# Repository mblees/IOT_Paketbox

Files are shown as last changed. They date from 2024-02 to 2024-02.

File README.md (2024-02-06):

# IoT-Projekt – Paketbox Dokumentation
WhatsApp Bild 2024-02-06 um 20 36 11_9b5375aa

## Übersicht:

### 1. Hardware
   #### 1.1 Box
   Das Gerüst der Paketbox besteht aus MiniTec-Aluprofilen, die zum Halten von 4 mm dicken Spanholzplatten genutzt werden. Der Deckel wird durch 2 Scharniere mit dem Körper der Box verbunden.

   #### 1.2 Sensoren/andere Hardware
   - Ultraschallsensor: HC-SR04
       - Da der Sensor auf 5V läuft und die GPIO-Pins des ESP32 nur 3,3V vertragen, muss ein Spannungsteiler bestehend aus 2 10k Ohm Widerständen verwendet werden. Das senkt die Spannung allerdings nicht genau auf 3,3V, deshalb muss in der Software damit gerechnet werden.
   - Reed-Modul: KY-021
       - Wird mit 3,3V versorgt, daher muss hier nichts Besonderes beachtet werden.
   - Schrittmotor: 28BYJ-48
       - Wird mit 5V über den dazugehörigen Motortreiber versorgt.
   - Matrixtastatur: [Link zur Tastatur](https://www.az-delivery.de/products/4x4-matrix-keypad)
       - Aufgrund mangelnder Pins verwende ich die 4x4 Matrix nur als 2x2 Matrix mit den Tasten 1, 2, 4, 5.
   - Stromversorgung durch eine Powerbank mit 5V Ausgang.

   #### 1.3 Mikroprozessor
   Beim Mikroprozessor handelt es sich um den WiFi-LoRa-32-V2 der Firma Heltec Automation mit eingebautem LoRa-Modul, Display und integrierter LED. Um Energie zu sparen, werden sowohl das Display als auch die integrierte LED nicht verwendet.

   #### 1.4 Verschlussmechanismus
   Der Verschlussmechanismus besteht aus einem Stepper Motor mit einem Zahnrad, welches einen Kolben durch 2 Ösen schiebt. Die Ösen sind jeweils am Deckel oder am Körper der Box befestigt und verhindern, wenn der Kolben ausgefahren ist, dass sich der Deckel öffnen lässt.
   
  WhatsApp Bild 2024-02-06 um 20 21 44_378a7dea

   Anmerkung: Hier handelt es sich Budgetbedingt um 3D-gedruckte Teile welche in eienr realen Anwendung nicht sicher genug wären um ein Paket mit Wert zu sichern.

### 2. Software
   #### 2.1 C++-Part / Mikroprozessorprogrammierung
   Die Programmierung des Controllers beruht auf dem Framework/Example LMIC-node von lnlp ([GitHub-Link](https://github.com/lnlp/LMIC-node)). Ich habe eine logische Steuerung in der `main()`-Funktion hinzugefügt sowie Bibliotheken für alle Peripheriekomponenten:
   - `Matrix.h`/`Matrix.cpp`: Beinhaltet das Auslesen der Matrix-Tastatur unter Verwendung der Bibliothek: `chris--a/Keypad@^3.1.1`.
   - `Reed_sensor.h`/`Reed_sensor.cpp`: Beinhaltet das Auslesen des Reed-Sensors, das über ein DigitalReed geschieht.
   - `Rfid.h`/`Rfid.cpp`: Beinhaltet Funktionen, um einen RFID-Sensor zu verwenden. Diese Funktion wurde letztendlich nicht genutzt, da der Mikrocontroller nicht genug Pins übrig hat.
   - `Stepper.h`/`Stepper.cpp`: Beinhaltet die Ansteuerung des Schrittmotor-Treibers unter Verwendung der Bibliothek: `waspinator/AccelStepper@^1.64`.
   - `Supersonic_sensor.h`/`Supersonic_sensor.cpp`: Beinhaltet das Auswerten des Ultraschallsensors und eine Funktion, die einen Mittelwert bildet, da der Sensor ab und zu falsche Werte liefern kann.

   #### 2.2 Python Service
   Der Service nutzt die HomeAssistantAPI, um Push-Benachrichtigungen an Handys zu schicken und die `paho-mqtt`-Bibliothek, um die von TTN empfangenen LoRa-Daten auszuwerten und daraufhin einen `notify`-Service in HomeAssistant auszulösen.
   
   notify

   #### 2.3 HomeAssistant
   Der HomeAssistant Server läuft in meinem Fall auf einer Oracle VM VirtualBox auf dem selben PC auf welchem auch der Python Service läuft. Die beiden Programme sind allerdings nur in soweit anhängig voneienander, dass sie im selben Wlan ausgeführt werden müssen.
   
   

### 3. Datenübertragung
   Die Daten, die mit den Sensoren erfasst werden, werden beim Öffnen und Schließen der Box vom Mikrocontroller über LoRa und The Things Network (TTN) gesendet. TTN stellt die Daten über einen MQTT-Server zur Verfügung, welche wir mithilfe eines Python-Services abfangen und daraufhin einen Service in HomeAssistant auslösen. Der Service in HomeAssistant führt dann wiederum dazu, dass eine Push-Benachrichtigung auf dem Handy des Besitzers der Box erscheint.

   Sensoren -> ESP32 -> LoRa -> TTN -> MQTT -> Python Service -> HomeAssistant -> Mobiltelefon

### 4. Pinbelegung


| Gerät | Pins |
|---|---|
| Matrixtastatur | 0, 2, 23, 25 |
| Steppermotor | 12, 13, 17, 21 |
| Reed Sensor | 36 |
| Ultraschallsensor | 22, 37 |
| LoRa Modul (Werk) | 19, 18, 5, 15, 4, 16, 26, 27, 14 |

### 5. Anmerkungen
Um weitere Features wie einen RFID-Sensor hinzuzufügen, fehlen dem verwendeten ESP32 weitere Pins. Eine mögliche Alternative war in diesem Fall der STM-WL55JC mit LoRa-Antenne. Allerdings gibt es für diesen Mikrocontroller keine öffentlichen LoRa-Bibliotheken, die für dieses Projekt in Frage gekommen wären. Ich habe versucht, eine Bibliothek für diesen Controller selbst zu schreiben, habe aber nach einigen Stunden Arbeit keine Ergebnisse erzielen können.

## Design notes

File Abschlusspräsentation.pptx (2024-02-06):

## Paketbox

Marius Blees

## Übersicht

- Hardware
- Software
- Datenübertragung
- Vorführung

Paketbox

## Hardware

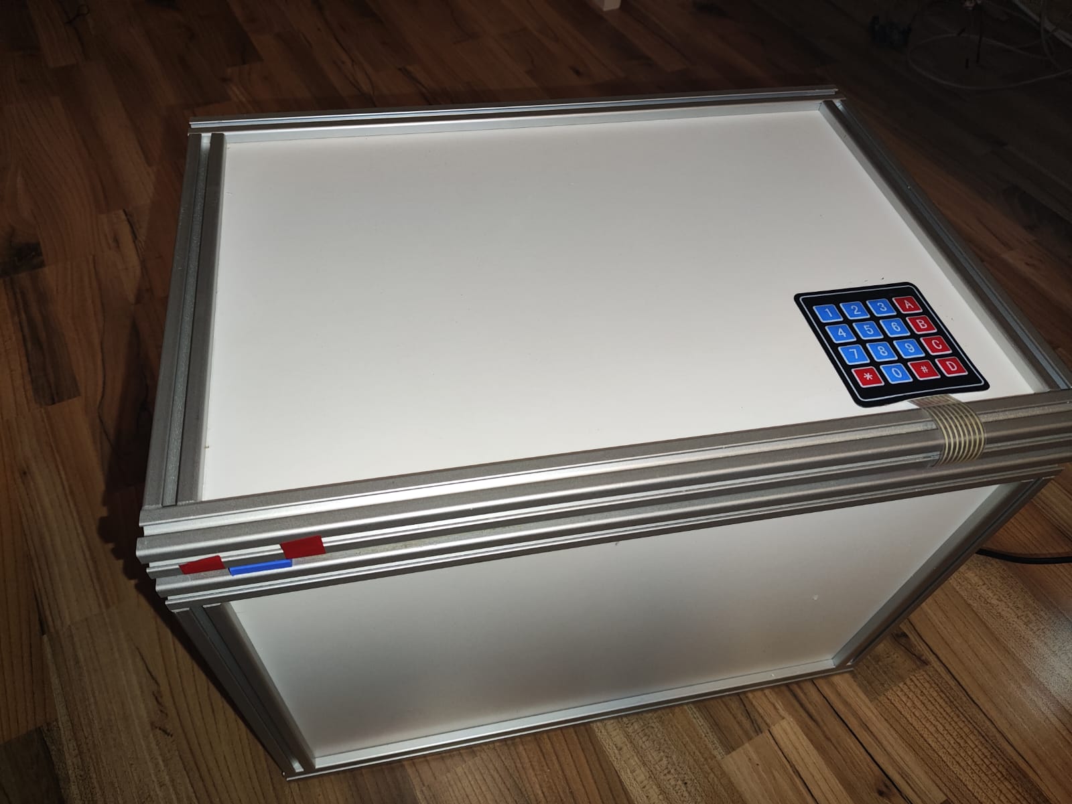
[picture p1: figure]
efe

Finales Aussehen der Paketbox

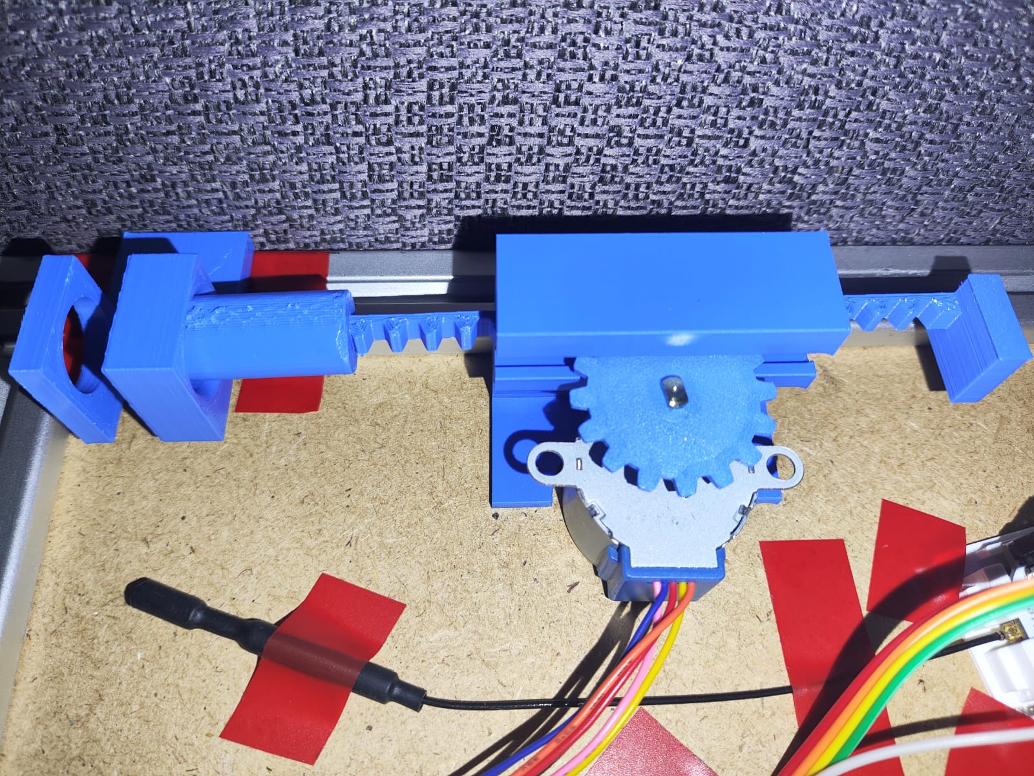
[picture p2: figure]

Verschlussmechanismus

## Hardware

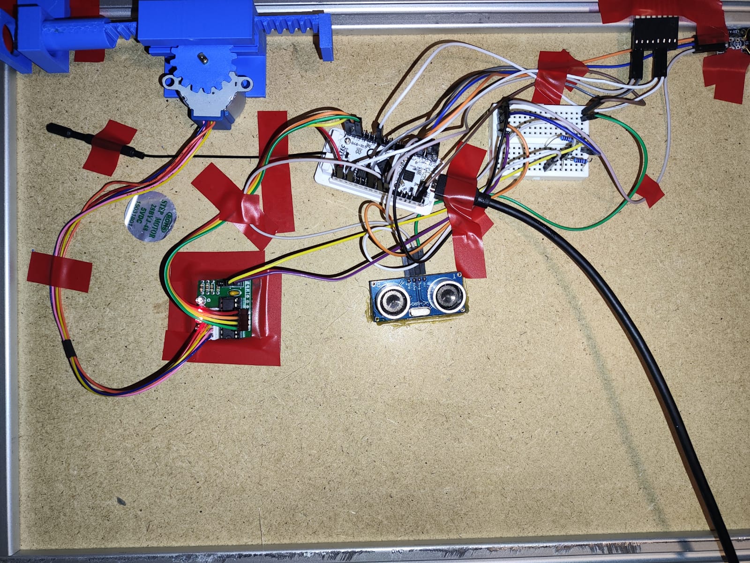
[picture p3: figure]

Verkabelung der Sensoren/Komponenten

## Software

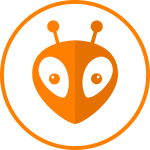
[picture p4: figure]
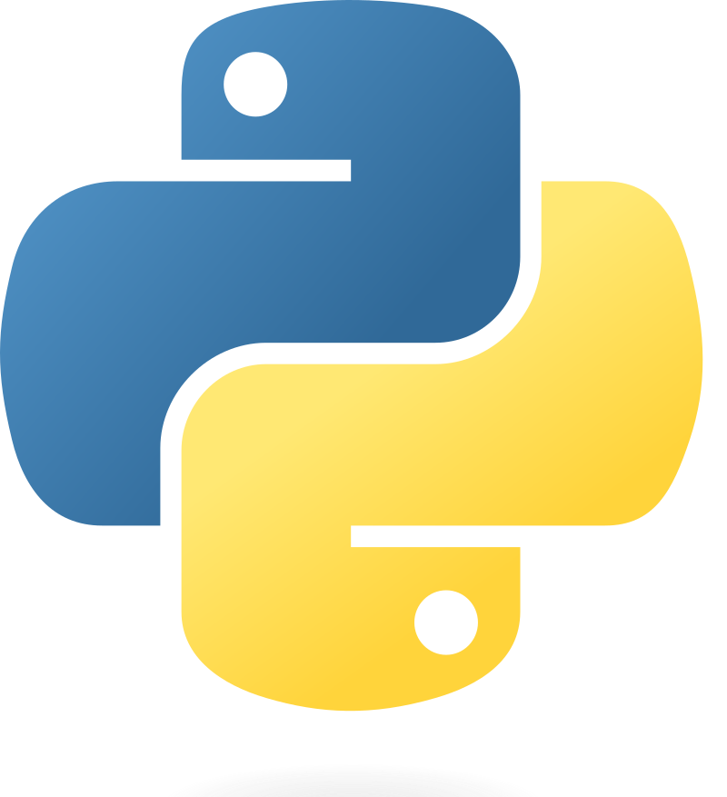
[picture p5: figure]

PlatformIO:
Programmierung in C++/ Arduino

Python:
als Service und Schnittstelle
zu HomeAssistant

## Datenübertragung

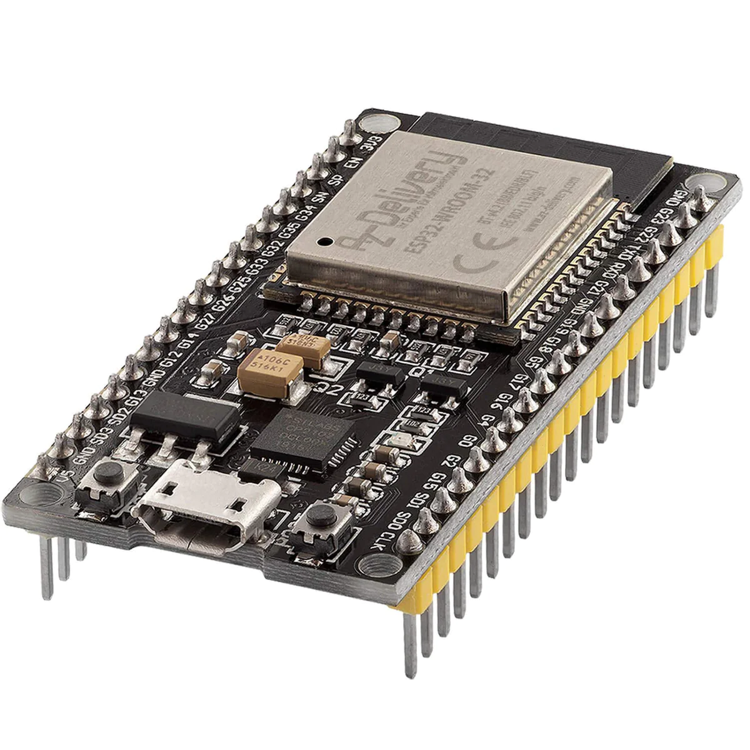
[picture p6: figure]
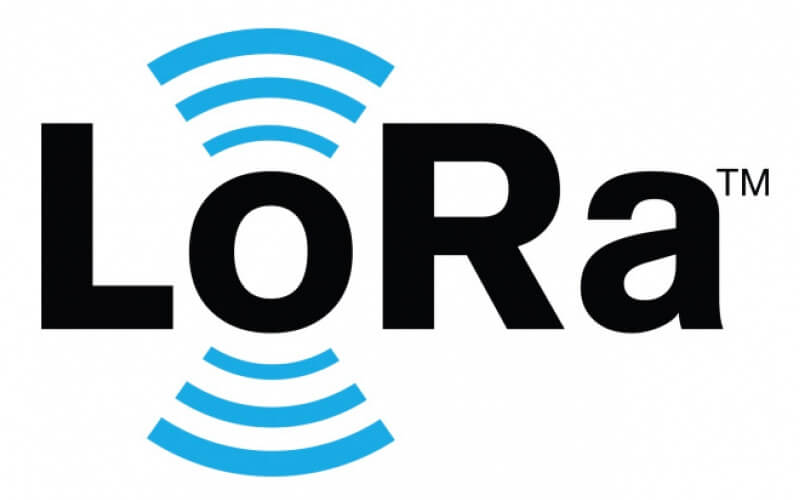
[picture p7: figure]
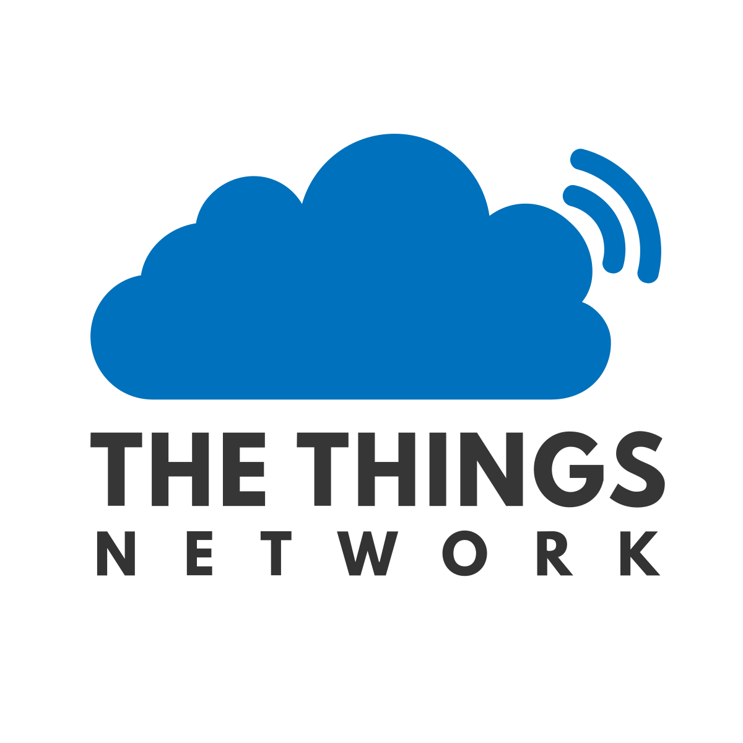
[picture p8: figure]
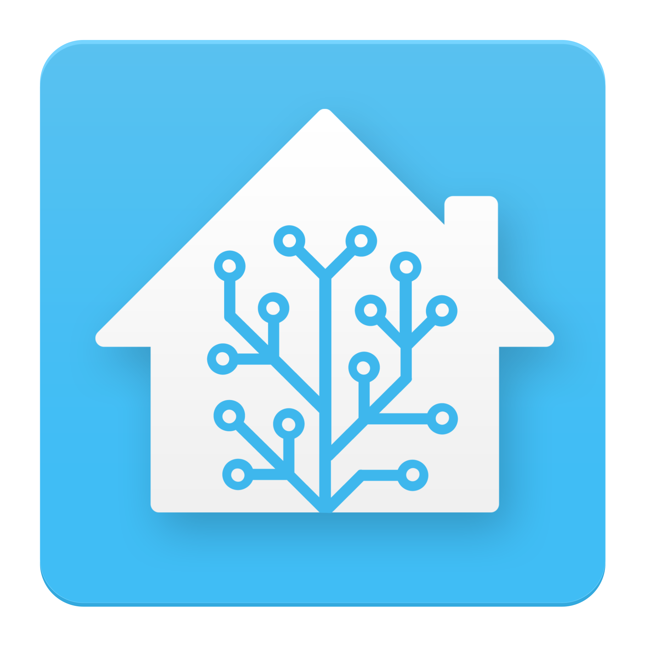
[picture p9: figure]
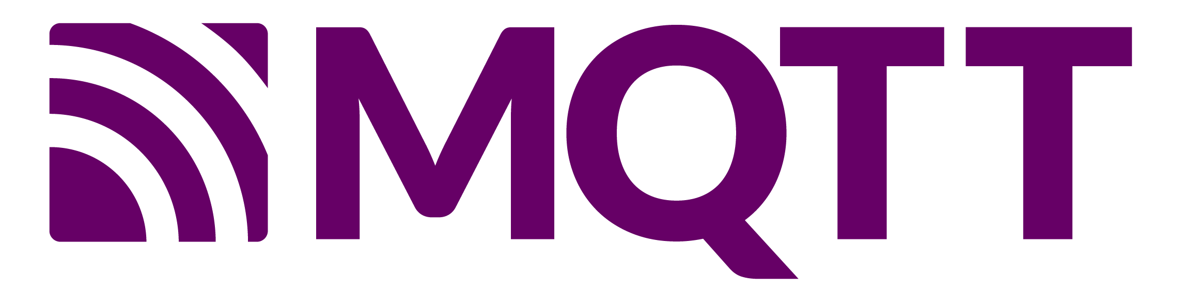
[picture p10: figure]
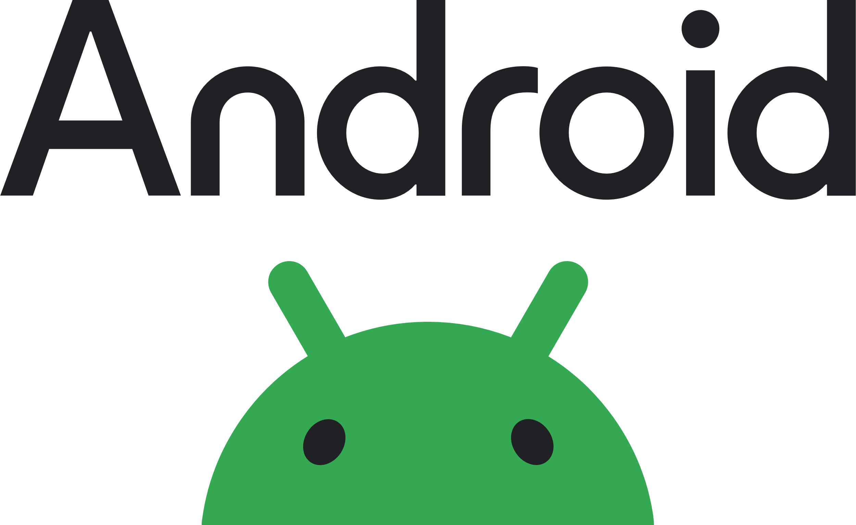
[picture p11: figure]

## VIELEN DANK

Gibt es noch Fragen?

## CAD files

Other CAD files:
Inventor/Adapter Stepper.ipt
Inventor/Connector MiniTec Counter.ipt
Inventor/Connector MiniTec.ipt
Inventor/Lineartranslator.ipt
Inventor/Schiene.ipt

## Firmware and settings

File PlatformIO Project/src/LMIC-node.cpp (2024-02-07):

/*******************************************************************************
 *
 *  File:          LMIC-node.cpp
 * 
 *  Function:      LMIC-node main application file.
 * 
 *  Copyright:     Copyright (c) 2021 Leonel Lopes Parente
 *                 Copyright (c) 2018 Terry Moore, MCCI
 *                 Copyright (c) 2015 Thomas Telkamp and Matthijs Kooijman
 *
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
 *                 THE SOFTWARE IS PROVIDED "AS IS", WITHOUT ANY WARRANTY.
 * 
 *  License:       MIT License. See accompanying LICENSE file.
 * 
 *  Author:        Leonel Lopes Parente
 * 
 *  Description:   To get LMIC-node up and running no changes need to be made
 *                 to any source code. Only configuration is required
 *                 in platform-io.ini and lorawan-keys.h.
 * 
 *                 If you want to modify the code e.g. to add your own sensors,
 *                 that can be done in the two area's that start with
 *                 USER CODE BEGIN and end with USER CODE END. There's no need
 *                 to change code in other locations (unless you have a reason).
 *                 See README.md for documentation and how to use LMIC-node.
 * 
 *                 LMIC-node uses the concepts from the original ttn-otaa.ino 
 *                 and ttn-abp.ino examples provided with the LMIC libraries.
 *                 LMIC-node combines both OTAA and ABP support in a single example,
 *                 supports multiple LMIC libraries, contains several improvements
 *                 and enhancements like display support, support for downlinks,
 *                 separates LoRaWAN keys from source code into a separate keyfile,
 *                 provides formatted output to serial port and display
 *                 and supports many popular development boards out of the box.
 *                 To get a working node up and running only requires some configuration.
 *                 No programming or customization of source code required.
 * 
 *  Dependencies:  External libraries:
 *                 MCCI LoRaWAN LMIC library  https://github.com/mcci-catena/arduino-lmic
 *                 IBM LMIC framework         https://github.com/matthijskooijman/arduino-lmic  
 *                 U8g2                       https://github.com/olikraus/u8g2
 *                 EasyLed                    https://github.com/lnlp/EasyLed
 *
 ******************************************************************************/

#include "LMIC-node.h"


//  █ █ █▀▀ █▀▀ █▀▄   █▀▀ █▀█ █▀▄ █▀▀   █▀▄ █▀▀ █▀▀ ▀█▀ █▀█
//  █ █ ▀▀█ █▀▀ █▀▄   █   █ █ █ █ █▀▀   █▀▄ █▀▀ █ █  █  █ █
//  ▀▀▀ ▀▀▀ ▀▀▀ ▀ ▀   ▀▀▀ ▀▀▀ ▀▀  ▀▀▀   ▀▀  ▀▀▀ ▀▀▀ ▀▀▀ ▀ ▀
#include "reed_sensor.h"
#include "supersonic_sensor.h"
#include "rfid.h"
#include "stepper.h"
#include "matrix.h"

const uint8_t payloadBufferLength = 4;    // Adjust to fit max payload length


//  █ █ █▀▀ █▀▀ █▀▄   █▀▀ █▀█ █▀▄ █▀▀   █▀▀ █▀█ █▀▄
//  █ █ ▀▀█ █▀▀ █▀▄   █   █ █ █ █ █▀▀   █▀▀ █ █ █ █
//  ▀▀▀ ▀▀▀ ▀▀▀ ▀ ▀   ▀▀▀ ▀▀▀ ▀▀  ▀▀▀   ▀▀▀ ▀ ▀ ▀▀ 

bool sendNotfication = false;
uint8_t payloadBuffer[payloadBufferLength];
static osjob_t doWorkJob;
uint32_t doWorkIntervalSeconds = DO_WORK_INTERVAL_SECONDS;  // Change value in platformio.ini

// Note: LoRa module pin mappings are defined in the Board Support Files.

// Set LoRaWAN keys defined in lorawan-keys.h.
#ifdef OTAA_ACTIVATION
    static const u1_t PROGMEM DEVEUI[8]  = { OTAA_DEVEUI } ;
    static const u1_t PROGMEM APPEUI[8]  = { OTAA_APPEUI };
    static const u1_t PROGMEM APPKEY[16] = { OTAA_APPKEY };
    // Below callbacks are used by LMIC for reading above values.
    void os_getDevEui (u1_t* buf) { memcpy_P(buf, DEVEUI, 8); }
    void os_getArtEui (u1_t* buf) { memcpy_P(buf, APPEUI, 8); }
    void os_getDevKey (u1_t* buf) { memcpy_P(buf, APPKEY, 16); }    
#else
    // ABP activation
    static const u4_t DEVADDR = ABP_DEVADDR ;
    static const PROGMEM u1_t NWKSKEY[16] = { ABP_NWKSKEY };
    static const u1_t PROGMEM APPSKEY[16] = { ABP_APPSKEY };
    // Below callbacks are not used be they must be defined.
    void os_getDevEui (u1_t* buf) { }
    void os_getArtEui (u1_t* buf) { }
    void os_getDevKey (u1_t* buf) { }
#endif


int16_t getSnrTenfold()
{
    // Returns ten times the SNR (dB) value of the last received packet.
    // Ten times to prevent the use of float but keep 1 decimal digit accuracy.
    // Calculation per SX1276 datasheet rev.7 §6.4, SX1276 datasheet rev.4 §6.4.
    // LMIC.snr contains value of PacketSnr, which is 4 times the actual SNR value.
    return (LMIC.snr * 10) / 4;
}


int16_t getRssi(int8_t snr)
{
    // Returns correct RSSI (dBm) value of the last received packet.
    // Calculation per SX1276 datasheet rev.7 §5.5.5, SX1272 datasheet rev.4 §5.5.5.

    #define RSSI_OFFSET            64
    #define SX1276_FREQ_LF_MAX     525000000     // per datasheet 6.3
    #define SX1272_RSSI_ADJUST     -139
    #define SX1276_RSSI_ADJUST_LF  -164
    #define SX1276_RSSI_ADJUST_HF  -157

    int16_t rssi;

    #ifdef MCCI_LMIC

        rssi = LMIC.rssi - RSSI_OFFSET;

    #else
        int16_t rssiAdjust;
        #ifdef CFG_sx1276_radio
            if (LMIC.freq > SX1276_FREQ_LF_MAX)
            {
                rssiAdjust = SX1276_RSSI_ADJUST_HF;
            }
            else
            {
                rssiAdjust = SX1276_RSSI_ADJUST_LF;   
            }
        #else
            // CFG_sx1272_radio    
            rssiAdjust = SX1272_RSSI_ADJUST;
        #endif    
        
        // Revert modification (applied in lmic/radio.c) to get PacketRssi.
        int16_t packetRssi = LMIC.rssi + 125 - RSSI_OFFSET;
        if (snr < 0)
        {
            rssi = rssiAdjust + packetRssi + snr;
        }
        else
        {
            rssi = rssiAdjust + (16 * packetRssi) / 15;
        }
    #endif

    return rssi;
}


void printEvent(ostime_t timestamp, 
                const char * const message, 
                PrintTarget target = PrintTarget::All,
                bool clearDisplayStatusRow = true,
                bool eventLabel = false)
{
    #ifdef USE_DISPLAY 
        if (target == PrintTarget::All || target == PrintTarget::Display)
        {
            display.clearLine(TIME_ROW);
            display.setCursor(COL_0, TIME_ROW);
            display.print(F("Time:"));                 
            display.print(timestamp); 
            display.clearLine(EVENT_ROW);
            if (clearDisplayStatusRow)
            {
                display.clearLine(STATUS_ROW);    
            }
            display.setCursor(COL_0, EVENT_ROW);               
            display.print(message);
        }
    #endif  
    
    #ifdef USE_SERIAL
        // Create padded/indented output without using printf().
        // printf() is not default supported/enabled in each Arduino core. 
        // Not using printf() will save memory for memory constrainted devices.
        String timeString(timestamp);
        uint8_t len = timeString.length();
        uint8_t zerosCount = TIMESTAMP_WIDTH > len ? TIMESTAMP_WIDTH - len : 0;

        if (target == PrintTarget::All || target == PrintTarget::Serial)
        {
            printChars(serial, '0', zerosCount);
            serial.print(timeString);
            serial.print(":  ");
            if (eventLabel)
            {
                serial.print(F("Event: "));
            }
            serial.println(message);
        }
    #endif   
}           

void printEvent(ostime_t timestamp, 
                ev_t ev, 
                PrintTarget target = PrintTarget::All, 
                bool clearDisplayStatusRow = true)
{
    #if defined(USE_DISPLAY) || defined(USE_SERIAL)
        printEvent(timestamp, lmicEventNames[ev], target, clearDisplayStatusRow, true);
    #endif
}


void printFrameCounters(PrintTarget target = PrintTarget::All)
{
    #ifdef USE_DISPLAY
        if (target == PrintTarget::Display || target == PrintTarget::All)
        {
            display.clearLine(FRMCNTRS_ROW);
            display.setCursor(COL_0, FRMCNTRS_ROW);
            display.print(F("Up:"));
            display.print(LMIC.seqnoUp);
            display.print(F(" Dn:"));
            display.print(LMIC.seqnoDn);        
        }
    #endif

    #ifdef USE_SERIAL
        if (target == PrintTarget::Serial || target == PrintTarget::All)
        {
            printSpaces(serial, MESSAGE_INDENT);
            serial.print(F("Up: "));
            serial.print(LMIC.seqnoUp);
            serial.print(F(",  Down: "));
            serial.println(LMIC.seqnoDn);        
        }
    #endif        
}      


void printSessionKeys()
{    
    #if defined(USE_SERIAL) && defined(MCCI_LMIC)
        u4_t networkId = 0;
        devaddr_t deviceAddress = 0;
        u1_t networkSessionKey[16];
        u1_t applicationSessionKey[16];
        LMIC_getSessionKeys(&networkId, &deviceAddress, 
                            networkSessionKey, applicationSessionKey);

        printSpaces(serial, MESSAGE_INDENT);    
        serial.print(F("Network Id: "));
        serial.println(networkId, DEC);

        printSpaces(serial, MESSAGE_INDENT);    
        serial.print(F("Device Address: "));
        serial.println(deviceAddress, HEX);

        printSpaces(serial, MESSAGE_INDENT);    
        serial.print(F("Application Session Key: "));
        printHex(serial, applicationSessionKey, 16, true, '-');

        printSpaces(serial, MESSAGE_INDENT);    
        serial.print(F("Network Session Key:     "));
        printHex(serial, networkSessionKey, 16, true, '-');
    #endif
}


void printDownlinkInfo(void)
{
    #if defined(USE_SERIAL) || defined(USE_DISPLAY)

        uint8_t dataLength = LMIC.dataLen;
        // bool ackReceived = LMIC.txrxFlags & TXRX_ACK;

        int16_t snrTenfold = getSnrTenfold();
        int8_t snr = snrTenfold / 10;
        int8_t snrDecimalFraction = snrTenfold % 10;
        int16_t rssi = getRssi(snr);

        uint8_t fPort = 0;        
        if (LMIC.txrxFlags & TXRX_PORT)
        {
            fPort = LMIC.frame[LMIC.dataBeg -1];
        }        

        #ifdef USE_DISPLAY
            display.clearLine(EVENT_ROW);        
            display.setCursor(COL_0, EVENT_ROW);
            display.print(F("RX P:"));
            display.print(fPort);
            if (dataLength != 0)
            {
                display.print(" Len:");
                display.print(LMIC.dataLen);                       
            }
            display.clearLine(STATUS_ROW);        
            display.setCursor(COL_0, STATUS_ROW);
            display.print(F("RSSI"));
            display.print(rssi);
            display.print(F(" SNR"));
            display.print(snr);                
            display.print(".");                
            display.print(snrDecimalFraction);                      
        #endif

        #ifdef USE_SERIAL
            printSpaces(serial, MESSAGE_INDENT);    
            serial.println(F("Downlink received"));

            printSpaces(serial, MESSAGE_INDENT);
            serial.print(F("RSSI: "));
            serial.print(rssi);
            serial.print(F(" dBm,  SNR: "));
            serial.print(snr);                        
            serial.print(".");                        
            serial.print(snrDecimalFraction);                        
            serial.println(F(" dB"));

            printSpaces(serial, MESSAGE_INDENT);    
            serial.print(F("Port: "));
            serial.println(fPort);
   
            if (dataLength != 0)
            {
                printSpaces(serial, MESSAGE_INDENT);
                serial.print(F("Length: "));
                serial.println(LMIC.dataLen);                   
                printSpaces(serial, MESSAGE_INDENT);    
                serial.print(F("Data: "));
                printHex(serial, LMIC.frame+LMIC.dataBeg, LMIC.dataLen, true, ' ');
            }
        #endif
    #endif
} 


void printHeader(void)
{
    #ifdef USE_DISPLAY
        display.clear();
        display.setCursor(COL_0, HEADER_ROW);
        display.print(F("LMIC-node"));
        #ifdef ABP_ACTIVATION
            display.drawString(ABPMODE_COL, HEADER_ROW, "ABP");
        #endif
        #ifdef CLASSIC_LMIC
            display.drawString(CLMICSYMBOL_COL, HEADER_ROW, "*");
        #endif
        display.drawString(COL_0, DEVICEID_ROW, deviceId);
        display.setCursor(COL_0, INTERVAL_ROW);
        display.print(F("Interval:"));
        display.print(doWorkIntervalSeconds);
        display.print("s");
    #endif

    #ifdef USE_SERIAL
        serial.println(F("\n\nLMIC-node\n"));
        serial.print(F("Device-id:     "));
        serial.println(deviceId);            
        serial.print(F("LMIC library:  "));
        #ifdef MCCI_LMIC  
            serial.println(F("MCCI"));
        #else
            serial.println(F("Classic [Deprecated]")); 
        #endif
        serial.print(F("Activation:    "));
        #ifdef OTAA_ACTIVATION  
            serial.println(F("OTAA"));
        #else
            serial.println(F("ABP")); 
        #endif
        #if defined(LMIC_DEBUG_LEVEL) && LMIC_DEBUG_LEVEL > 0
            serial.print(F("LMIC debug:    "));  
            serial.println(LMIC_DEBUG_LEVEL);
        #endif
        serial.print(F("Interval:      "));
        serial.print(doWorkIntervalSeconds);
        serial.println(F(" seconds"));
        if (activationMode == ActivationMode::OTAA)
        {
            serial.println();
        }
    #endif
}     


#ifdef ABP_ACTIVATION
    void setAbpParameters(dr_t dataRate = DefaultABPDataRate, s1_t txPower = DefaultABPTxPower) 
    {
        // Set static session parameters. Instead of dynamically establishing a session
        // by joining the network, precomputed session parameters are be provided.
        #ifdef PROGMEM
            // On AVR, these values are stored in flash and only copied to RAM
            // once. Copy them to a temporary buffer here, LMIC_setSession will
            // copy them into a buffer of its own again.
            uint8_t appskey[sizeof(APPSKEY)];
            uint8_t nwkskey[sizeof(NWKSKEY)];
            memcpy_P(appskey, APPSKEY, sizeof(APPSKEY));
            memcpy_P(nwkskey, NWKSKEY, sizeof(NWKSKEY));
            LMIC_setSession (0x1, DEVADDR, nwkskey, appskey);
        #else
            // If not running an AVR with PROGMEM, just use the arrays directly
            LMIC_setSession (0x1, DEVADDR, NWKSKEY, APPSKEY);
        #endif

        #if defined(CFG_eu868)
            // Set up the channels used by the Things Network, which corresponds
            // to the defaults of most gateways. Without this, only three base
            // channels from the LoRaWAN specification are used, which certainly
            // works, so it is good for debugging, but can overload those
            // frequencies, so be sure to configure the full frequency range of
            // your network here (unless your network autoconfigures them).
            // Setting up channels should happen after LMIC_setSession, as that
            // configures the minimal channel set. The LMIC doesn't let you change
            // the three basic settings, but we show them here.
            LMIC_setupChannel(0, 868100000, DR_RANGE_MAP(DR_SF12, DR_SF7),  BAND_CENTI);      // g-band
            LMIC_setupChannel(1, 868300000, DR_RANGE_MAP(DR_SF12, DR_SF7B), BAND_CENTI);      // g-band
            LMIC_setupChannel(2, 868500000, DR_RANGE_MAP(DR_SF12, DR_SF7),  BAND_CENTI);      // g-band
            LMIC_setupChannel(3, 867100000, DR_RANGE_MAP(DR_SF12, DR_SF7),  BAND_CENTI);      // g-band
            LMIC_setupChannel(4, 867300000, DR_RANGE_MAP(DR_SF12, DR_SF7),  BAND_CENTI);      // g-band
            LMIC_setupChannel(5, 867500000, DR_RANGE_MAP(DR_SF12, DR_SF7),  BAND_CENTI);      // g-band
            LMIC_setupChannel(6, 867700000, DR_RANGE_MAP(DR_SF12, DR_SF7),  BAND_CENTI);      // g-band
            LMIC_setupChannel(7, 867900000, DR_RANGE_MAP(DR_SF12, DR_SF7),  BAND_CENTI);      // g-band
            LMIC_setupChannel(8, 868800000, DR_RANGE_MAP(DR_FSK,  DR_FSK),  BAND_MILLI);      // g2-band
            // TTN defines an additional channel at 869.525Mhz using SF9 for class B
            // devices' ping slots. LMIC does not have an easy way to define set this
            // frequency and support for class B is spotty and untested, so this
            // frequency is not configured here.
        #elif defined(CFG_us915) || defined(CFG_au915)
            // NA-US and AU channels 0-71 are configured automatically
            // but only one group of 8 should (a subband) should be active
            // TTN recommends the second sub band, 1 in a zero based count.
            // https://github.com/TheThingsNetwork/gateway-conf/blob/master/US-global_conf.json
            LMIC_selectSubBand(1);
        #elif defined(CFG_as923)
            // Set up the channels used in your country. Only two are defined by default,
            // and they cannot be changed.  Use BAND_CENTI to indicate 1% duty cycle.
            // LMIC_setupChannel(0, 923200000, DR_RANGE_MAP(DR_SF12, DR_SF7),  BAND_CENTI);
            // LMIC_setupChannel(1, 923400000, DR_RANGE_MAP(DR_SF12, DR_SF7),  BAND_CENTI);

            // ... extra definitions for channels 2..n here
        #elif defined(CFG_kr920)
            // Set up the channels used in your country. Three are defined by default,
            // and they cannot be changed. Duty cycle doesn't matter, but is conventionally
            // BAND_MILLI.
            // LMIC_setupChannel(0, 922100000, DR_RANGE_MAP(DR_SF12, DR_SF7),  BAND_MILLI);
            // LMIC_setupChannel(1, 922300000, DR_RANGE_MAP(DR_SF12, DR_SF7),  BAND_MILLI);
            // LMIC_setupChannel(2, 922500000, DR_RANGE_MAP(DR_SF12, DR_SF7),  BAND_MILLI);

            // ... extra definitions for channels 3..n here.
        #elif defined(CFG_in866)
            // Set up the channels used in your country. Three are defined by default,
            // and they cannot be changed. Duty cycle doesn't matter, but is conventionally
            // BAND_MILLI.
            // LMIC_setupChannel(0, 865062500, DR_RANGE_MAP(DR_SF12, DR_SF7),  BAND_MILLI);
            // LMIC_setupChannel(1, 865402500, DR_RANGE_MAP(DR_SF12, DR_SF7),  BAND_MILLI);
            // LMIC_setupChannel(2, 865985000, DR_RANGE_MAP(DR_SF12, DR_SF7),  BAND_MILLI);

            // ... extra definitions for channels 3..n here.
        #endif

        // Disable link check validation
        LMIC_setLinkCheckMode(0);

        // TTN uses SF9 for its RX2 window.
        LMIC.dn2Dr = DR_SF9;

        // Set data rate and transmit power (note: txpow is possibly ignored by the library)
        LMIC_setDrTxpow(dataRate, txPower);    
    }
#endif //ABP_ACTIVATION
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
void loop() 
{   

    const uint8_t password[4] = {'1', '2', '4', '5'};
    static uint8_t input[4] = {0x00, 0x00, 0x00, 0x00};
    static bool waitingforreset = false;

    char input_byte = getKey();
    static uint8_t input_index = 0;

    if(input_byte != ' ' && !waitingforreset){
        if(input_byte == '1'){
            input_index = 0;
            input[input_index] = input_byte;
            Serial.print("Input Reset: ");
            Serial.println(input_byte);
        }
        else{
            input_index++;
            input[input_index] = input_byte;
            Serial.print("Input Normal: ");
            Serial.println(input_byte);
        }
        if(input_index == 3){
            if(input[0] == password[0] && input[1] == password[1] && input[2] == password[2] && input[3] == password[3]){
                Serial.println("Password correct");
                open_door();
                Serial.println("Waiting for door to open...");
                delay(3000); //give user time to open door
                Serial.println("Door opened");
                waitingforreset = true;
                sendNotfication = true;
            }
            input_index = 0;
            input[0] = 0x00;
            input[1] = 0x00;
            input[2] = 0x00;
            input[3] = 0x00;
        }
    }
    if(waitingforreset && (read_reed() == 0)){
        Serial.println("Door closed");
        close_door();
        waitingforreset = false;
    }
    os_runloop_once();
}

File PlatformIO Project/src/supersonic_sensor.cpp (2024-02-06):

#include "supersonic_sensor.h"

void init_us()
{
    pinMode(us_trig_pin, OUTPUT);
    pinMode(us_echo_pin, INPUT);
}

float read_us()
{
    float duration = 0;
    float distance = 0;

    digitalWrite(us_trig_pin, LOW);
    delayMicroseconds(2);

    digitalWrite(us_trig_pin, HIGH);
    delayMicroseconds(12);

    digitalWrite(us_trig_pin, LOW);

    duration = pulseIn(us_echo_pin, HIGH);
    distance = (duration * 0.0343) / 2;

    if (distance > MAX_DISTANCE || distance <= 0)
    {
        return -1;
    }
    else
    {
        return distance;
    }
}

float read_us_average(){
    float distance = 0;
    float additive = 0;
    uint8_t confirmation_counter = 0;

    for(int i = 0; i <= 10; i++){
        additive = read_us();
        if(additive == -1){
            i--;
            confirmation_counter++;
        }
        else{
            distance += additive;
        }
        if(confirmation_counter == 10){
            return -1;
        }
    }
    return distance / 10;
}

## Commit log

2024-02-05 added sensors
2024-02-05 added stepper lib
2024-02-06 added average for US-Sensor
